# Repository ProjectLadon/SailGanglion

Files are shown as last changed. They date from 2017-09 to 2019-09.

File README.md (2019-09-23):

# SailGanglion
This is the brains of each sail. This covers the electronics, sensors, and software for each sail. The master branch is currently devoted to the subscale test vessel; future variants will get their own branches. 

## Required Design Properties
* Continuously controls the orientation of the tail of each wing in response to commands.
* Tail orientation commanded +/- 30 degrees of neutral
* Battery powered
* Uses rosserial over WiFi for all communications
* Subscribes to tail commands
* Publishes sail heading commands

## Electronic Hardware Components
* Adafruit Feather Huzzah ESP8266 (https://www.adafruit.com/product/2821)
* Hitec HS-82MG Servo (https://hitecrcd.com/products/servos/micro-and-mini-servos/analog-micro-and-mini-servos/hs-82mg/product)
* Sparkfun MPU-9250 Breakout (https://www.sparkfun.com/products/13762)

## Mechanical Design
The sail was designed in Fusion 360. There will be a link here...

## Libraries
* rosserial (https://github.com/ros-drivers/rosserial)
* Sparkfun MPU-9650 DMP library, modified for ESP compatibility (https://github.com/rupin/SparkFun_MPU-9250-DMP_Arduino_Library)

## Pinout
* I2C pins -- per standard (GPIO4 & GPIO5)
* Servo PWM -- GPIO2
* Foresail Select (pull down) -- GPIO14
* Mizzen Select (pull down) -- GPIO12
* Leave foresail and mizzen select pins floating for single-sail operation

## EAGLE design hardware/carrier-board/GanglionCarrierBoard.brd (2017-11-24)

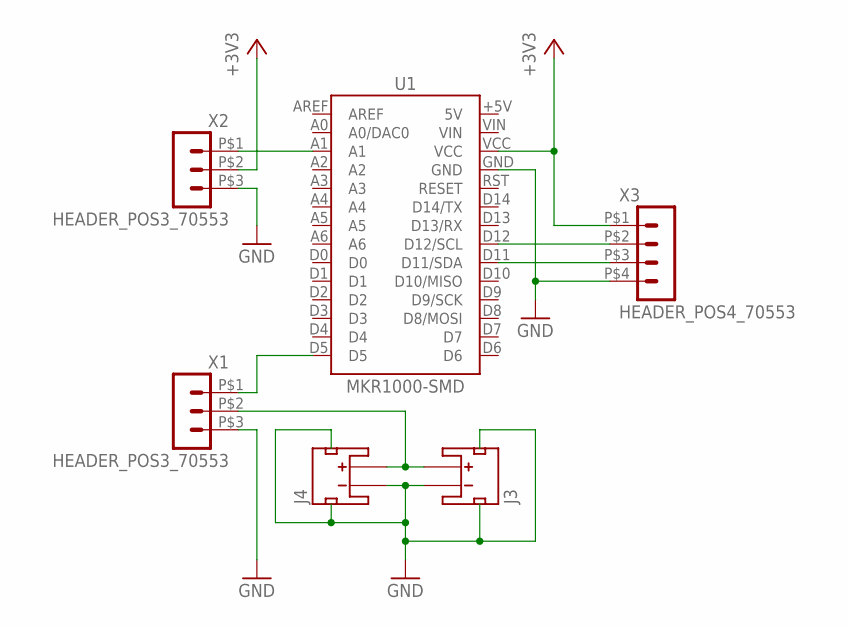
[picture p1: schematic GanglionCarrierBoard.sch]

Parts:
J3, J4: JST_2MM_MALE; JST-2-SMD
U1: MKR1000-SMD
X1, X2: HEADER_POS3_70553; 70553-POS3
X3: HEADER_POS4_70553; 70553-POS4

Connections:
+3V3: U1.VCC, X2.P$2 (2), X3.P$1 (1)
GND: J3.1 (-), J3.NC1 (PAD1), J3.NC2 (PAD2), J4.1 (-), J4.NC1 (PAD1), J4.NC2 (PAD2), U1.GND, X1.P$3 (3), X2.P$3 (3), X3.P$4 (4)
unnamed: U1.A1, X2.P$1 (1)
unnamed: U1.D5, X1.P$1 (1)
unnamed: J3.2 (+), J4.2 (+), X1.P$2 (2)
unnamed: U1.D12 (D12/SCL), X3.P$2 (2)
unnamed: U1.D11 (D11/SDA), X3.P$3 (3)

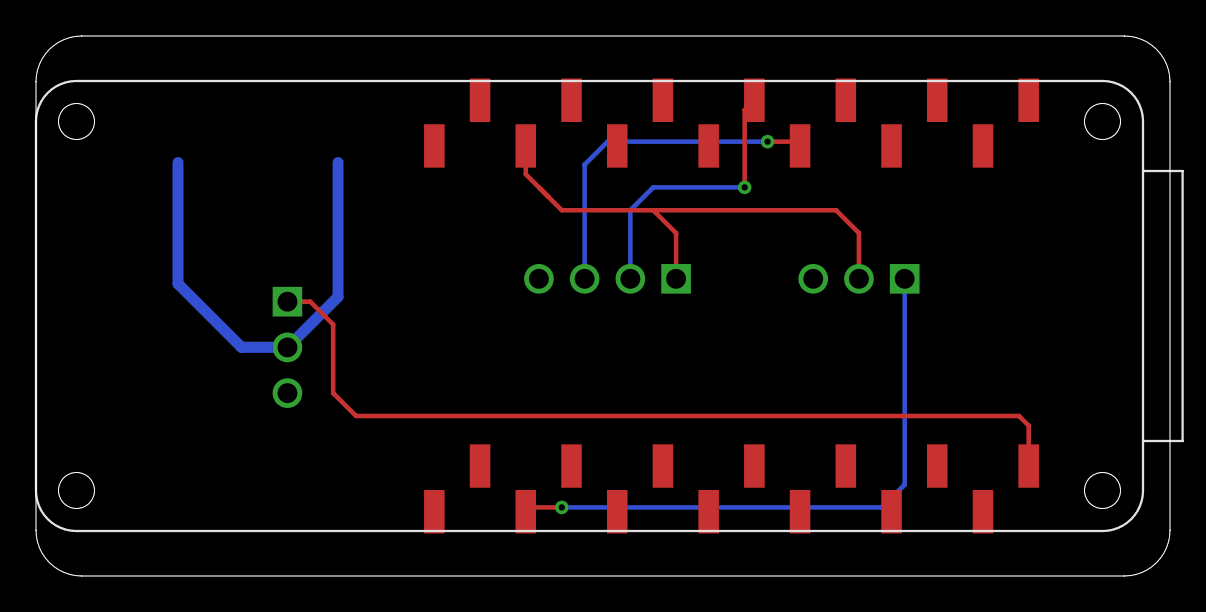
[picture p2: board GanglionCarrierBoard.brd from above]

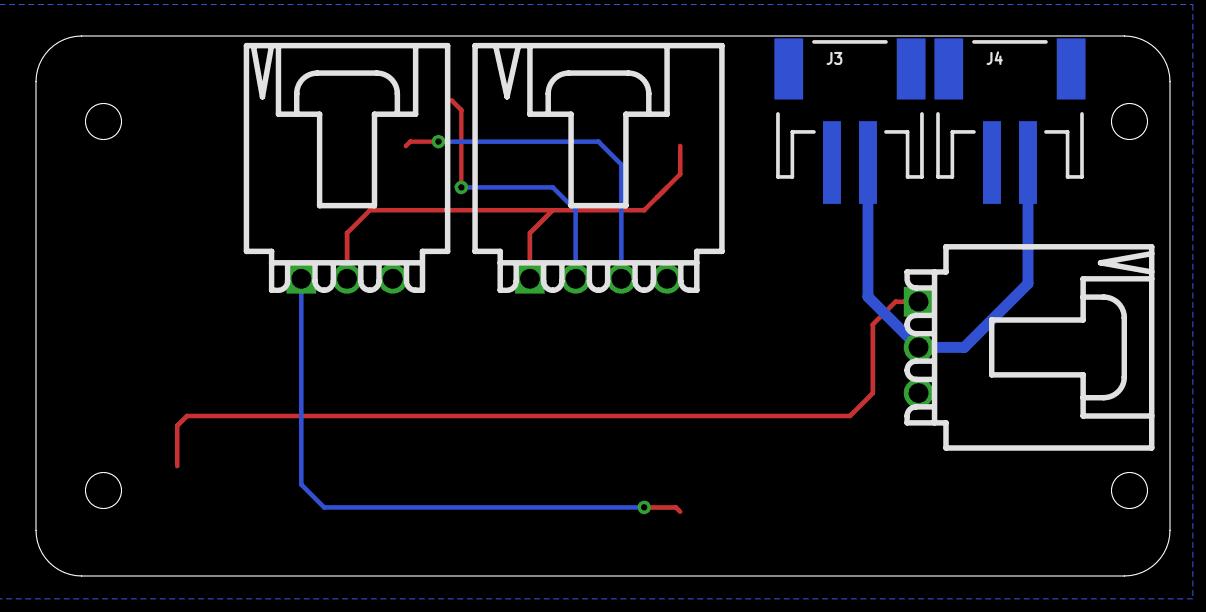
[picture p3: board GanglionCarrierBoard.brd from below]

Board: 2 copper layers, 63.0 x 30.0 mm, 6 parts (5 on the bottom side), 7 nets.

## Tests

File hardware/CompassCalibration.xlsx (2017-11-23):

 | X |  | Y |  | Z
 | max | min | max | min | max | min
Foresail limits | 3879 | -1386 | 5934 | 1574 | 12535 | 5586
 | X | Y | Z
Foresail Offsets | -1246.5 | -3754 | -9060.5
Foresail Gains | 0.0380 | 0.0459 | 0.0288
 | X |  | Y |  | Z
 | max | min | max | min | max | min
Mizzen Limits | 5976 | 468 | 6414 | 1811 | 5142 | -2844
 | X | Y | Z
Mizzen Offsets | -3222 | -4112.5 | -1149
Mizzen Gains | 0.0363 | 0.0434 | 0.0250

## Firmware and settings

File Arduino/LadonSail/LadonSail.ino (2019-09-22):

//#define DEBUG_MODE  (1)

#define ESP8266

#include <Servo.h>
#include <SparkFunMPU9250-DMP.h>
#include <ESP8266WiFi.h>
#include <ros.h>
#include <std_msgs/Float32.h>

/* 
* Sail mode is selected by tieing pin to gnd. Pins are pulled up internally.
* Single-sail mode is selected if both pins are left floating.
* Tieing both pins to gnd will halt the process.
*/
#define FORESAIL_SELECT_PIN  (14)
#define MIZZEN_SELECT_PIN    (12)

#define SAIL_SERVO_PIN  (2)
#define COMPASS_MAG_ADDRESS (0x1e)
#define COMPASS_ACC_ADDRESS (0x68)
//#define AOA_PIN   (A0)
//#define AOA_PWR   (A1)
//#define AOA_GND   (A2)
//#define IMU_PWR   (10)
//#define IMU_GND   (9)

// IP Addresses
IPAddress foresailIP(192,168,8,90);
IPAddress mizzenIP(192,168,8,91);
IPAddress ros_server(192,168,8,1);
IPAddress netmask(255,255,255,0);
const uint16_t ros_port = 11411;

// IMU object & addresses
#define AHRS true         // Set to false for basic data read
MPU9250_DMP imu;
bool imuGood = false;

// Status
int status = WL_IDLE_STATUS;

// Create ROS messages and pointers for subscribers and publishers
ros::NodeHandle     nh;
std_msgs::Float32   cmd_msg;
std_msgs::Float32   hdg_msg;
std_msgs::Float32   tail_msg;
ros::Publisher*     hdg_publisher;
ros::Publisher*     tail_publisher;
ros::Subscriber<std_msgs::Float32>* cmd_subscriber;

// WiFi parameters
char ssid[] = "BeagleBone-DEB1";
char password[] = "BeagleBone";

// Declare functions to be exposed to the API
void tail_callback(const std_msgs::Float32& cmd);

// Declare sail write function
bool sailWrite (int cmd);

// Create Servo instance
Servo sail;
#define SERVO_OFFSET  (90)
#define SERVO_RANGE   (45)

void setup(void) {
  // Start Serial
  Serial.begin(115200);

  // start servo
  sail.attach(SAIL_SERVO_PIN);
  sail.write(SERVO_OFFSET);

  // turn on LED output
  pinMode(LED_BUILTIN, OUTPUT);
  digitalWrite(LED_BUILTIN, LOW);
  delay(1000);

  if (Serial) Serial.println("I live!");
    
  if (imu.begin() != INV_SUCCESS) {
    while (1)
    {
      if (Serial) Serial.println("Unable to communicate with MPU-9250");
      if (Serial) Serial.println("Check connections, and try again.");
      if (Serial) Serial.println();
      delay(5000);
    }
  }
  imu.dmpBegin(DMP_FEATURE_6X_LP_QUAT | // Enable 6-axis quat
               DMP_FEATURE_GYRO_CAL, // Use gyro calibration
               10);

  /* Explicitly set the ESP8266 to be a WiFi-client, otherwise, it by default,
     would try to act as both a client and an access-point and could cause
     network-issues with your other WiFi-devices on your WiFi-network. */
  WiFi.mode(WIFI_STA);
  
  // Check if we are foresail or mizzen
  // Create ROS publishers and subscribers
  pinMode(FORESAIL_SELECT_PIN, INPUT_PULLUP);
  pinMode(MIZZEN_SELECT_PIN, INPUT_PULLUP);

  // Foresail only mode
  if (digitalRead(FORESAIL_SELECT_PIN) == LOW && digitalRead(MIZZEN_SELECT_PIN) == HIGH) {
    WiFi.config(foresailIP, ros_server, netmask);
    static ros::Subscriber<std_msgs::Float32> tailsub("/foresail/cmd", tail_callback);
    static ros::Publisher hdgpub("/foresail/heading", &hdg_msg);
    static ros::Publisher tailpub("/foresail/tail", &tail_msg);
    cmd_subscriber = &tailsub;
    hdg_publisher = &hdgpub;
    tail_publisher = &tailpub;
    if (Serial) Serial.println("Foresail");

  // Mizzen only mode
  } else if (digitalRead(FORESAIL_SELECT_PIN) == HIGH && digitalRead(MIZZEN_SELECT_PIN) == LOW) {
    WiFi.config(mizzenIP, ros_server, netmask);
    static ros::Subscriber<std_msgs::Float32> tailsub("/mizzen/cmd", tail_callback);
    static ros::Publisher hdgpub("/foresail/heading", &hdg_msg);
    static ros::Publisher tailpub("/foresail/tail", &tail_msg);
    cmd_subscriber = &tailsub;
    hdg_publisher = &hdgpub;
    tail_publisher = &tailpub;
    if (Serial) Serial.println("Mizzen");

  // Single-sail mode
  } else if (digitalRead(FORESAIL_SELECT_PIN) == HIGH && digitalRead(MIZZEN_SELECT_PIN) == HIGH) {
    if (Serial) Serial.println("Single-sail");
    // TODO: Define single-sail mode behavior
    // Loop here forever
    for (;;) {} 

  // Illegal mode, both selection pins pulled low
  } else {
    if (Serial) Serial.println("Illegal mode selection");

    // TODO: Define failsafe behavior for illegal mode selection
    // Loop here forever
    for (;;) {} 
  }

  // Connect to WiFi
  while (status != WL_CONNECTED) {
    if (Serial) Serial.print("Attempting to connect to SSID: ");
    if (Serial) Serial.println(ssid);
    status = WiFi.begin(ssid, password);

    // Wait 1 seconds for connection:
    delay(1000);
  }
  if (Serial) Serial.println("WiFi connected");
  digitalWrite(LED_BUILTIN, HIGH);

  // Print the IP address
  IPAddress ip = WiFi.localIP();
  if (Serial) Serial.print("IP Address: ");
  if (Serial) Serial.println(ip);

  // Start ROS
  nh.getHardware()->setConnection(ros_server, ros_port);
  nh.initNode();
  nh.advertise(*hdg_publisher);
  nh.advertise(*tail_publisher);
  nh.subscribe(*cmd_subscriber);

}

void loop() {

  // trigger IMU processing 
  if ( imu.fifoAvailable() ) {
    // Use dmpUpdateFifo to update the ax, gx, mx, etc. values
    if ( imu.dmpUpdateFifo() == INV_SUCCESS) {
      // computeEulerAngles can be used -- after updating the
      // quaternion values -- to estimate roll, pitch, and yaw
      //if (Serial) Serial.println("Getting compass data...");
      imu.computeEulerAngles();
      hdg_msg.data = 360 - imu.yaw;
    }
  }

  // check for connection, reconnect if missing
  if (WiFi.status() == WL_CONNECTED) {
    //digitalWrite(LED_BUILTIN, HIGH);
  } else {
    digitalWrite(LED_BUILTIN, LOW);
    if (Serial) Serial.println("Lost WiFi connection");
    if (Serial) Serial.print("Wifi status is: ");
    if (Serial) Serial.println(WiFi.status());
    WiFi.begin(ssid, password);
    delay(100);
    return;
  }

  // ROS publication
  hdg_publisher->publish(&hdg_msg);
  tail_publisher->publish(&tail_msg);

  // ROS Spin
  nh.spinOnce();
  delay(50);

  return;
}

// Custom function accessible by the API
void tail_callback(const std_msgs::Float32& cmd) {

  // Get state from command
  if (Serial) Serial.print("Incoming command: ");
  if (Serial) Serial.println(cmd.data);
  int cmd_int = (int)(cmd.data + SERVO_OFFSET);
  if (sailWrite(cmd_int)) {
    tail_msg.data = cmd_int;
  } else tail_msg.data = 0;
}

// Sail writing command
bool sailWrite(int cmd) {
  if (cmd > (SERVO_OFFSET + SERVO_RANGE)) cmd = (SERVO_OFFSET + SERVO_RANGE);
  if (cmd < (SERVO_OFFSET - SERVO_RANGE)) cmd = (SERVO_OFFSET - SERVO_RANGE);
  if (Serial) Serial.print("Executing command "); if (Serial) Serial.println(cmd);
  sail.write(cmd);
  return true;
}

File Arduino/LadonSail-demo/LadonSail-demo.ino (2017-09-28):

//#define DEBUG_MODE  (1)

#include <Servo.h>
#include <SPI.h>
#include <WiFi101.h>
#include <aREST.h>
#include <Wire.h>
#include <WiFiUdp.h>

#define PROG_PIN  (0)
#define SAIL_PIN  (3)
#define COMPASS_MAG_ADDRESS (0x1e)
#define COMPASS_ACC_ADDRESS (0x68)
#define UDP_PORT  (13000)

// IP Addresses
IPAddress foresailIP(192,168,0,90);
IPAddress mizzenIP(192,168,0,91);
IPAddress controllerIP(192,168,0,92);

// Status
int status = WL_IDLE_STATUS;

// Create aREST instance
aREST rest = aREST();

// WiFi parameters
char ssid[] = "Underworld";
char password[] = "divedivedive";

// The port to listen for incoming TCP connections
#define LISTEN_PORT           80

// Create an instance of the server
//WiFiServer server(LISTEN_PORT);
//WiFiUDP Udp;

// Declare functions to be exposed to the API
int servoControl(String command);

// Declare sail write function
bool sailWrite (int cmd);

// Create Servo instance
Servo sail;
#define SERVO_OFFSET  (90)
#define SERVO_RANGE   (30)

// Create variables for aREST
float aoa = 0;
float sailHeading = 0;

void setup(void)
{
  
  // Check if we are foresail or mizzen
  // Give name and ID to device
  pinMode(PROG_PIN, INPUT);
  if  (digitalRead(PROG_PIN) == HIGH) {
    rest.set_id("1");
    rest.set_name("foresail");
    WiFi.config(foresailIP);
  } else {
    rest.set_id("2");
    rest.set_name("mizzen");
    WiFi.config(mizzenIP);
  }

  sail.attach(SAIL_PIN);
  sail.write(90);
}

void loop() {
  sail.write(90);
  delay(15000);
  sail.write(105);
  delay(15000);
  sail.write(120);
  delay(15000);
  sail.write(75);
  delay(15000);
  sail.write(60);
  delay(15000);
  
}

// Custom function accessible by the API
int servoControl(String command) {

  // Get state from command
  if (Serial) Serial.print("Incoming command: ");
  if (Serial) Serial.println(command);
  int cmd = command.toInt();
  if (sailWrite(cmd)) {
    return cmd;
  } else return 0;
}

// Sail writing command
bool sailWrite(int cmd) {
  if (cmd > (SERVO_OFFSET + SERVO_RANGE)) return false;
  if (cmd < (SERVO_OFFSET - SERVO_RANGE)) return false;
  sail.write(cmd);
  return true;
}

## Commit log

2017-08-29 Updated README.md
    Now with hardware links. Still don't have a great one for the AOA sensor, since that's custom.
2017-09-01 Fixed and stable, still taking inputs in degrees. TODO: add input bounds checking
    [LadonSail.ino]
2017-09-28 Fixed excessively short delay on receive, added LED feedback and reconnection to wifi
    [LadonSail.ino]
2017-11-23 Working Software
    [CompassCalibration.xlsx]
2017-11-24 Added a design for the carrier board
    [GanglionCarrierBoard.brd, GanglionCarrierBoard.sch]
2019-05-05 Set ROS connection correctly
    [LadonSail.ino]

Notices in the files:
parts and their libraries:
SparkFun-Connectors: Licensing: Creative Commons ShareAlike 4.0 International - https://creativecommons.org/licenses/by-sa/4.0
